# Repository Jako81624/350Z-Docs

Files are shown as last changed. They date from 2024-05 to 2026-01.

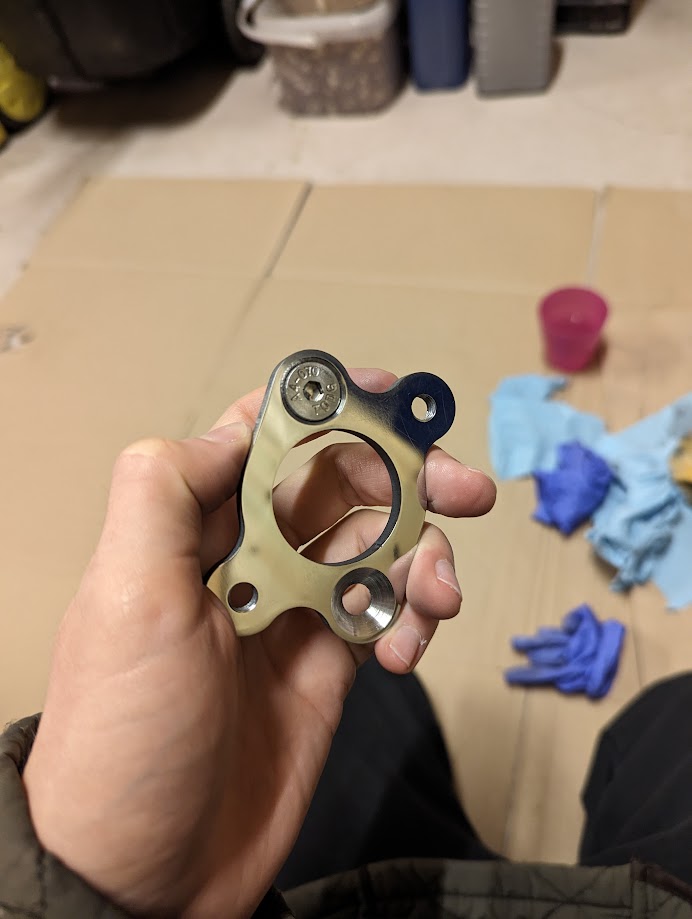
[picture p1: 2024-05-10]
Clutch-System/Master-Cylinder/Adapter-Plate-Front.jpg

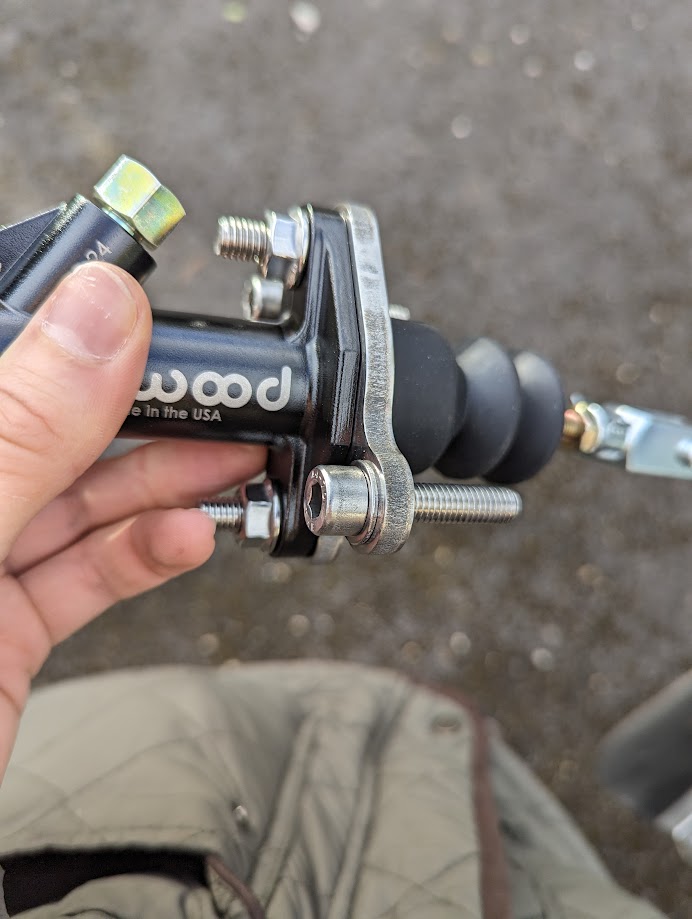
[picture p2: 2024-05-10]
Clutch-System/Master-Cylinder/Adapter-Plate-Rear.jpg

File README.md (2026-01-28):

# 350Z-Docs
Progressive documentation for undocumented areas of the 350Z - designed to increase longevity and democratize modification

When it comes to car modification, there is very little documentation for the little things.  A lot of crucial elements have been measured hundreds of times by many hundreds of people, but, for a variety of reasons, ranging from enclosure by private companies to sheer forgetfulness on the part of the individual, these crucial little tidbits are not public knowledge.

This repository was created purely with the intention of documenting all those useful bits and pieces.  If you have anything to add, please fork the repo and make a pull request.  Any additions are very much appreciated.

All files inside this repository are licensed under the Creative Commons CC-BY-SA 4.0 license (https://creativecommons.org/licenses/by-sa/4.0/) unless otherwise confirmed in direct correspondence with the repository creator.

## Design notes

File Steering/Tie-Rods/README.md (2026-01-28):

# HA (High-Adjust) Tie Rods
The files in this directory consist of all the components required to fabricate an outer tie rod (tie rod end) for the 350Z platform.

This is a somewhat novel design.  The shank component is inserted into the spindle and is secured by one flanged M12x1.25 nut (STEP file included under "Nuts", ISO standard).  This nut should be torqued to *at least* 34Nm in accordance to the FSM.  It is the opinion of some manufacturers that this is not enough torque, but without further testing I cannot take an educated stance.  One of the features of this design is a vertical, unthreaded section above the conical seat that extends to approximately one millimetre below the surface of the spindle.  This _should_ prevent catastrophic failure from over-torquing, but it is *NOT* a target, nor should it be relied on to prevent this.  There is a groove cut above the thread to house an 8mm E or C clip to prevent steering loss in the even that the retaining nut should back out.  It is *critical* that a thread locking compound is used with this retaining nut - "blue" strength compounds are recommended.  I recommend using the threaded misalignment spacers as jam nuts to torque down the retaining bolt.

**IMPORTANT NOTE** - The 350Z spindle is made from aluminium.  Over-torquing of the shank MAY result in the conical seat being dragged through the spindle receptacle, snapping it in half.  Older vehicles that have undergone many fatigue cycles (or have had replacement tie rod ends installed "enthusiastically" in the past) may have weakened receptacles.  Aluminium does not have a fatigue limit - any load applied will result in cumulative damage.  For all aluminium parts, failure is "when" and not "if".  For this reason, as of writing I recommend using the torque specification listed in the FSM (34Nm) and applying threadlocker.  Please check that this nut remains secure at several occasions less than 100 miles post-install, for the safety of yourself and others.

The turnbuckle is longer than most aftermarket offerings (as far as I am aware) at 95mm.  This is with the intention of ensuring maximum strength and thread engagement, but some edge cases may not be compatible.  If this is the case for you, the turnbuckle can be shortened by the requisite amount from the end housing the M14 thread in CAD.  One end is threaded for M14x1.5 - the thread diameter and pitch of the 350Z inner tie rods.  The other is threaded for M16x2.0.  Most 16mm-eye metric rod-end bearings on the market are built to this specification, as was the case for my chosen bearing; the SKF SAKAC 16M.  I encourage end users to use serviceable components - bearing coatings do not last forever and greasing them instead at your yearly inspection is easily done.  An M16x2.0 jam nut (ISO-4035 spec recommended) is required to "lock" the rod-end in to the turnbuckle.  A STEP file is provided under "Nuts".

The final components are the so-called "threaded misalignment spacers".  These are what make this kit "high-adjust".  There are two nuts - the top is thinner, the bottom thicker.  Both have an 18 degree chamfer on the flat face of one side.  The top nut is threaded on first with the chamfer on the underside.  This is followed by installing the rod-end bearing onto the 16mm shaft.  Finally, the bottom nut is installed with the chamfer on the topside (against the bearing).  These two nuts can then be adjusted to change the position of the rod-end bearing, which in turn will affect your steering geometry and "bump steer".  To eliminate bump steer to the best of your ability, ensure that your tie rods sit parallel with your lower control arms when the car is sat at ride height.  I do not yet know how far offset the bearing should be from the bottom of the spindle for a stock vehicle, but respected manufacturers (SPL) have it listed at half an inch, so I would start around there (18mm seems to be a close equivalent in comparison).  These documents will be updated when I have a more concrete measurement.

The TMS's do not have a torque spec other than *tight*.  Threadlocker is, once again, critical for safety.  Use it on the bottom TMS, even if you don't on the top.  In my case, SKF does not list a maximum compressive force for their bearings, and my material of choice was Grade 5 Titanium so I will be targeting 75Nm.  The only risk you face is deforming the bearing or shearing the shank in half.  Proceed with care!  Other fasteners under radial loads in the suspension area (brake caliper bolts, for example) are secured with bolts set to 88.3Nm, and the compression arms are secured at 84.5Nm.  Keep in mind that any inferences I make from that are purely "vibes-based", but that level of torque _feels_ suitable.

Addendum: The reason for the chamfer on the TMS's is to allow for maximum bearing misalignment.  The SAKAC 16M that I'm using has a rated misalignment of 15 degrees, so I made the chamfers at 18 degrees to allow the nuts to handily clear the bearing race.

## Material Choices
As previously mentioned, I used Grade 5 Titanium when making mine.  Other manufacturers have used 4000-grade alloy steels for theirs, and I can only assume that Nissan does something similar.  In the FEA that I carried out, I saw a single stress concentrator at or exceeding 950Mpa on the shank under the worst conditions imaginable (excessive pressure, unrealistic and enormous torque arm).  This is almost certainly an FEA artifact, but without further testing I can't confirm anything.  As such, I would err on the side of caution and use a material that exceeds 500Mpa.  I wouldn't expect loads to exceed even 200Mpa when used with under realistic installation conditions, but again, this is all theoretical.  Be safe and err on the side of caution.

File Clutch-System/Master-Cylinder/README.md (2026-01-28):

# Master Cylinder Adapter Plate
This adapter plate adapts the stock 350Z CMC mounting location (70mm PCD, 30deg off-centre) to the vertically aligned Wilwood/Tilton type mounts.

If all you want is the adapter, send the DXF file to your laser cutting service of choice (6mm thick steel or metal of your choice).  You will need to tap the off-centre holes (firewall holes) for an M8 thread and countersink the vertically aligned holes (on the side against the firewall) as to both mount the aftermarket cylinder to the adapter using countersunk M8 head-socket bolts and to install two 30 or 35mm fully-threaded M8 socket head bolts into your freshly tapped threads (I recommend some blue threadlock to stop them backing out) and install the assembled unit in the stock location.  Pictures are in the repo for guidance.

It is likely that the fit in the bolt holes will be tight.  Persevere, it will install snug.

You will almost certainly need to replace the stock clutch line to accomodate an aftermarket CMC.  Measurements and fittings for those lines are in Hydraulic-Lines folder one directory up from here.  If in doubt, use a banjo bolt.

CC-BY-SA 4.0

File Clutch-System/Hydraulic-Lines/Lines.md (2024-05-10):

## Clutch Hydraulic Lines
When upgrading the clutch, it is quite common that supplemental modification to the hydraulic components will be required too.  In regards to the HR-generation, the CSC (Concentric Slave Cylinder) is known to have a limited lifespan - though replacing it with an aftermarket unit tends to rememdy this issue, and some aftermarket clutch manufacturers create kits that are designed for use with OEM/OEM-Style CSCs (OS Giken, for example).

TODO: Add dimensions and sketch of slave cylinder

At the other end of the system is the master cylinder.  Details below:

    DE+:
        Bore: 
        - 5/8"in

    HR:
        Bore: 
        - 11/16"in

    All:
        Thread Size and Pitch:
        - M10x1.0
        Clutch Feed Hose Size:
        - 8AN

TODO: Move these to their own dedicated section

The clutch lines in the 350Z are notorious for being difficult to bleed.  This will lead a lot of people to replacing them.  In stock form, both the pre-HR and HR generation use four clutch lines.  The first leads to the clutch damper located in the front-left wheel-well behind the rearwards plastic shroud.  The second leads from the aformentioned damper, to a bracket underneath the car.  This bracket is what starts the third section - this time using flexible hose.  The final section is a short and arguably redunant hardline run that exits the flexible hose and performs a u-turn to go back into the CSC termination block.  As of writing, my experience is with the HR generation, and in this case the flexible hose is secured at both ends with horseshoe clips to a bracket on the chassis and the gearbox respectively.

The clutch lines are all threaded in M10x1.0.  When replacing the clutch lines, some will opt to replace only the soft line and leave the hardline in place.  There are many kits out there that achieve this, and, in the case of the HR, the length of the flexible section will be no longer than approximately 30cm (data sourced from UKDM RHD vehicle).

Hose Details:

    DE+:
        - Unknown, please fork and submit a pull req if known
    HR:
        Lengths:
            Short (Flexi):
            - Approx. 30cm
            Combined run (CMC to CSC termination block)
            - Approx. 228cm

        Fittings:
            Short (Flexi):
            - 2x Female M10x1.0 Circlip Fittings
            Short (Flexi to CSC termination block):
            - M10x.10 Male (Convex lip, flexi end) to M10x1.0 Male (Concave lip, termination block end)
            Hard Line (CMC to Damper)
            - M10x1.0 Male to M10x1.0 Male
            Hard Line (Damper to Flexi)
            - M10x1.0 Male to M10x1.0 Male

Many people will replace the master cylinder with an aftermarket unit when using heavier aftermarket clutches.  There is no adjustment to be made in hydraulic system.  Clutch "bite" and modulation is a function of the throw distance between the face of the CSC and your pressure plate and the bore/displacement of your master cylinder.  Clutch "weight" is a function of pressure plate strength and CSC/CMC bore.  This being said, it is *possible* to make some minor adjustments to the height of your clutch pedal by winding in the clevis on your master cylinder, and winding out either your upper clutch stopper on cars unequipped with cruise control or your clutch ASCD on cruise-equipped vehicles.  Both are located in the same place.  This will **NOT** change the characteristics of your clutch - just the height of your pedal.

There are a couple of methods by which you can adjust the modulation of your clutch. One is by changing the bore ratio between the CSC and CMC i.e. a smaller bore CMC will require less foot pressure and will displace less clutch fluid per unit distance.  The obvious warning here is that you will have to ensure that your CMC can displace _enough_ fluid to fully disengage your clutch, or you risk damaging your clutch and/or being unable to disengage the transmission from the engine entirely.  Displacement of the stock CMC is currently not documented, but based on aftermarket units I perform my calculations with 1.25" of travel.  The other option is to design a mechanism by which you can adjust the ratio of pedal to CMC plunger movement.  For example, attaching the CMC plunger closer to the point of pedal rotation would result in less lateral movement - however, this would have the unintended side-effect of actuating the plunger at an extreme angle and potentially accelerating wear significantly.  If a design comes to fruition, it will be documented here.

Common replacements for CMCs include both Tilton and Wilwood.  Dimensions are available from the manufacturer for fabricators.  Dimensions of the stock CMC will be included here when they have been obtained.  The PCD is larger than the Wilwood GS Remote as of the time of writing, and the firewall bolts appear to approximately be rotated at a 20 degree angle from the horizontal plane.  CAD drawings and adapter plates will be open sourced and included here when completed.

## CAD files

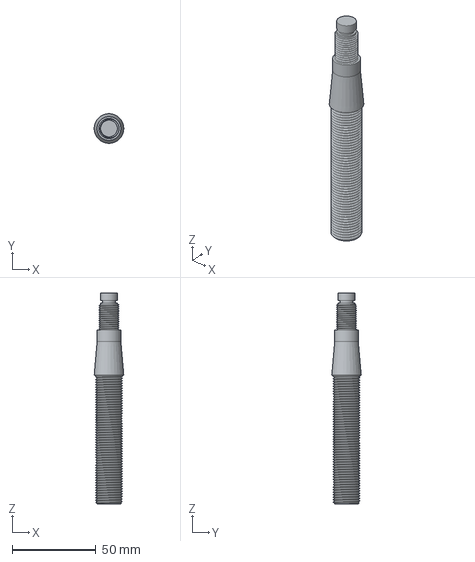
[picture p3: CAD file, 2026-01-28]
Steering/Tie-Rods/Shank/Shank-SingleCurve-FullThread.step
17.7 x 17.7 x 125.9 mm

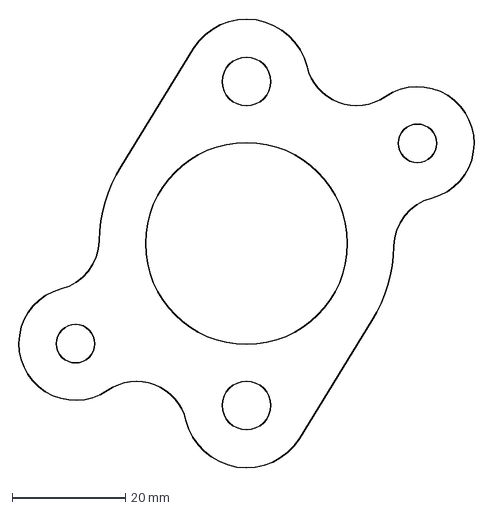
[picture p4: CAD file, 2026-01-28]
Clutch-System/Master-Cylinder/350ZMasterCylinderWilwoodAdapterV2-Sketch.dxf
81.4 x 80.3 mm

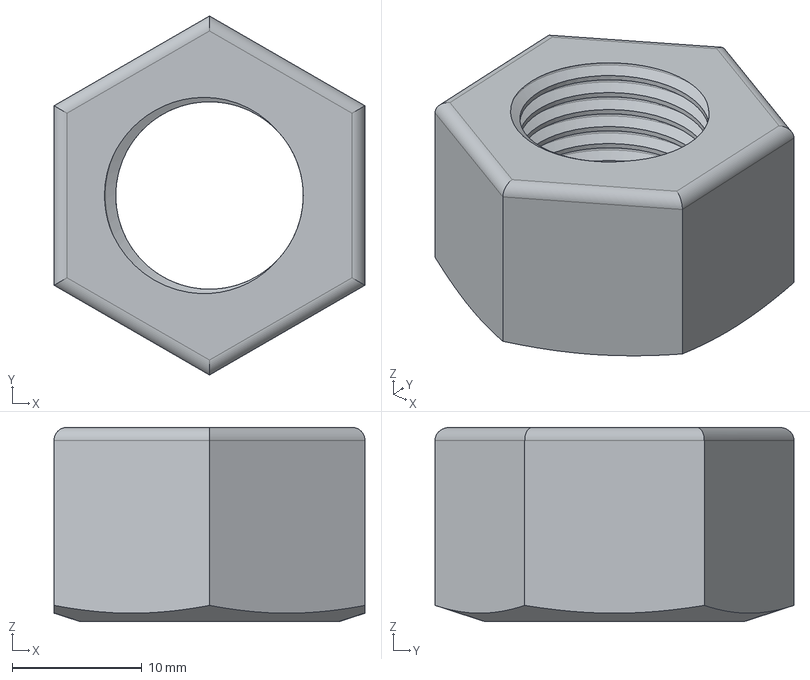
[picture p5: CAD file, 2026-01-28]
Steering/Tie-Rods/Misalignment Spacer/Bottom/CNC/Threaded Misalignment Spacer Bottom - CNC.step
24.0 x 27.7 x 15.0 mm

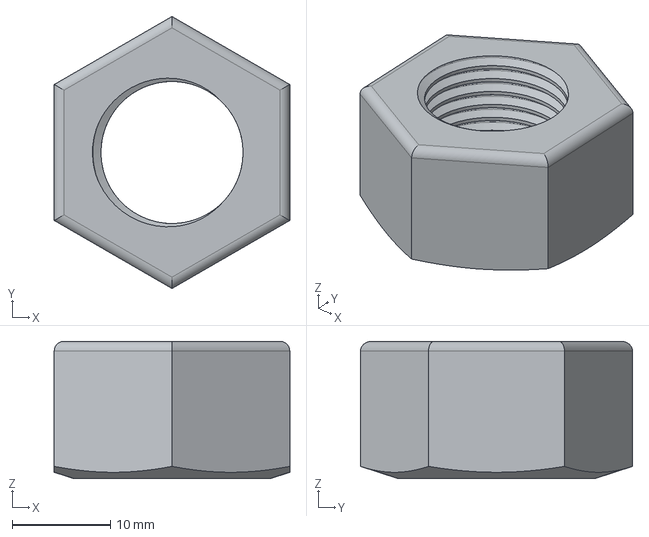
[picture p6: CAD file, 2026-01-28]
Steering/Tie-Rods/Misalignment Spacer/Bottom/Threaded Misalignment Spacer Bottom.step
24.0 x 27.7 x 14.0 mm

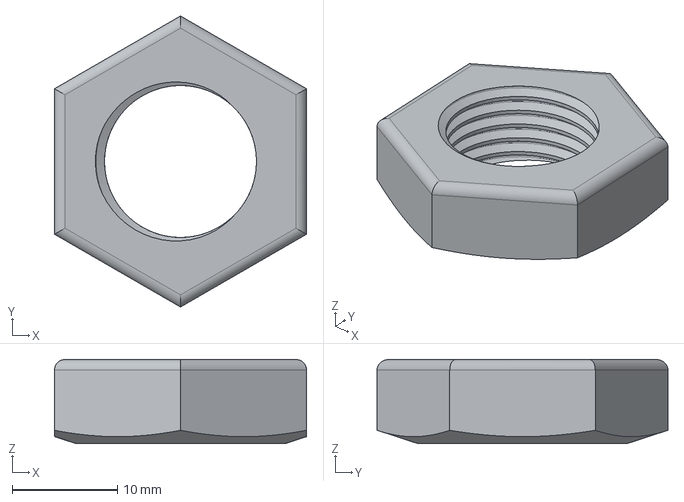
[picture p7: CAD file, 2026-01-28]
Steering/Tie-Rods/Misalignment Spacer/Top/CNC/Threaded Misalignment Spacer Top - CNC.step
24.0 x 27.7 x 8.00 mm

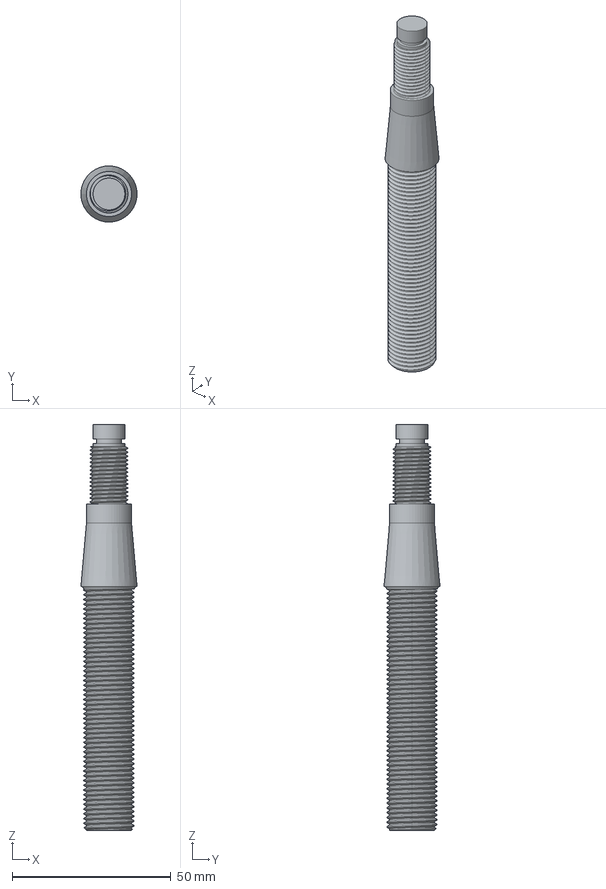
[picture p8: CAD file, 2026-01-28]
Steering/Tie-Rods/Shank/CNC/Shank-CNC.step
17.7 x 17.7 x 127.9 mm

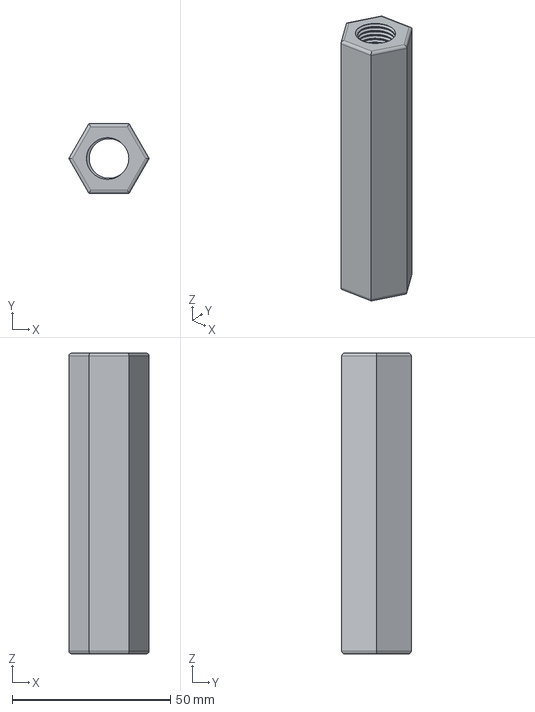
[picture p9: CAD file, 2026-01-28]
Steering/Tie-Rods/Turnbuckle/CNC/Turnbuckle-CNC.step
25.4 x 22.0 x 95.0 mm

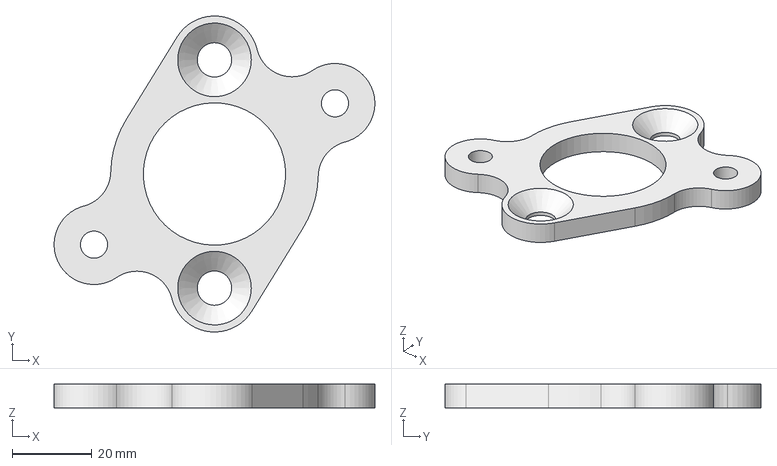
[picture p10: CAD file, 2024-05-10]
Clutch-System/Master-Cylinder/350ZMasterCylinderWilwoodAdapterV2.FCStd
80.4 x 79.2 x 6.00 mm

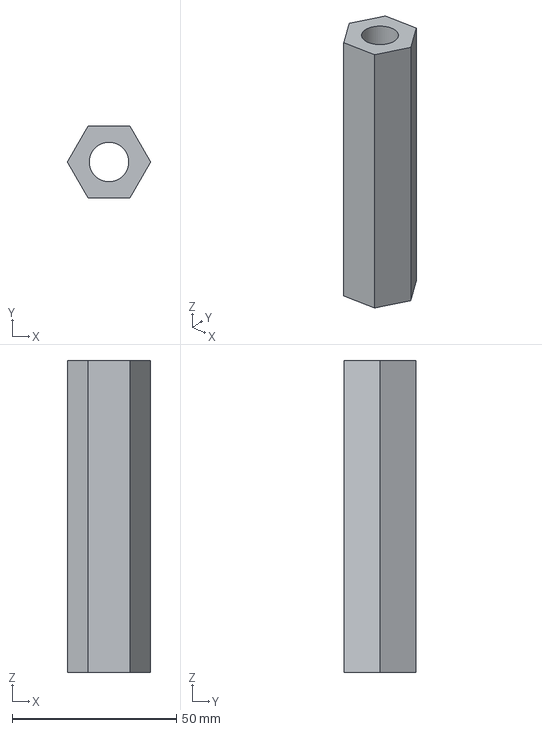
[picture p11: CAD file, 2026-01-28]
Steering/Tie-Rods/Turnbuckle/Turnbuckle-Unthreaded.step
25.4 x 22.0 x 95.0 mm

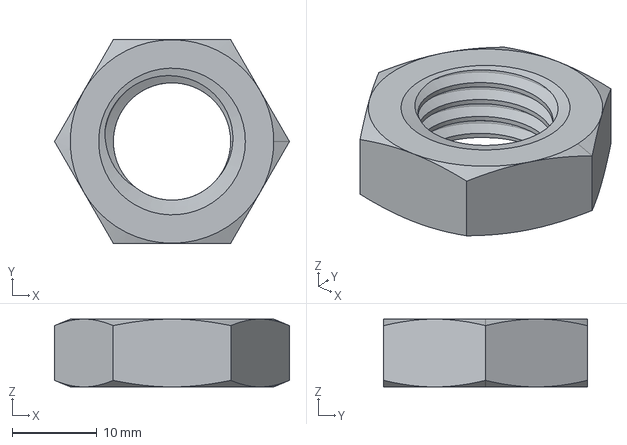
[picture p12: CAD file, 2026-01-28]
Steering/Tie-Rods/Nuts/M16x2.0-Nut-ISO4035.step
27.7 x 24.0 x 8.00 mm

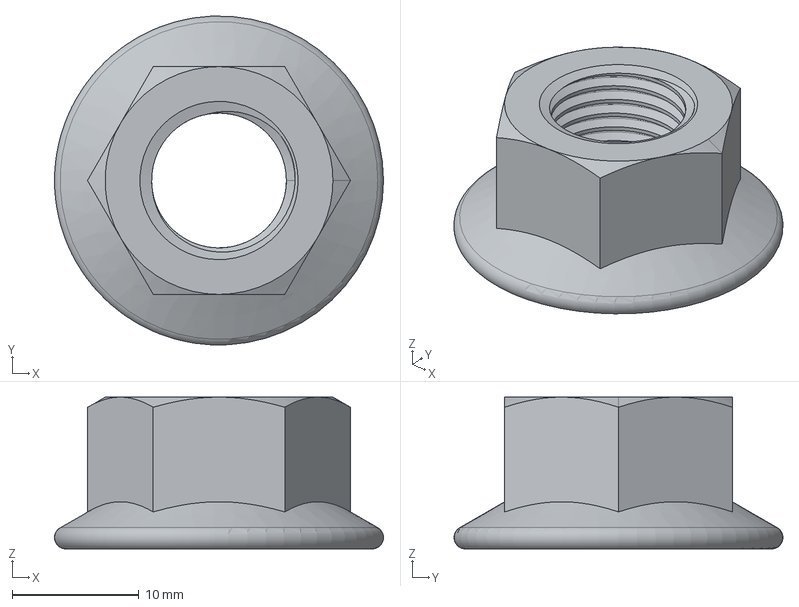
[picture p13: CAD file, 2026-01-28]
Steering/Tie-Rods/Nuts/M12x1.25-Nut-Flanged.step
26.0 x 26.0 x 12.0 mm

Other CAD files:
Steering/Tie-Rods/Misalignment Spacer/Top/Threaded Misalignment Spacer.FCStd
Steering/Tie-Rods/Shank/Shank.FCStd
Steering/Tie-Rods/Turnbuckle/Turnbuckle.FCStd
Steering/Tie-Rods/Misalignment Spacer/Top/Threaded Misalignment Spacer-Threaded.step
Clutch-System/Master-Cylinder/350ZMasterCylinderWilwoodAdapterV2-Chamfer.obj
Steering/Tie-Rods/Turnbuckle/Turnbuckle-Threaded.step
Steering/Tie-Rods/Misalignment Spacer/Bottom/CNC/Threaded Misalignment Spacer Bottom - CNC.FCStd
Steering/Tie-Rods/Misalignment Spacer/Bottom/Threaded Misalignment Spacer Bottom.FCStd
Steering/Tie-Rods/Misalignment Spacer/Top/CNC/Threaded Misalignment Spacer Top - CNC.FCStd
Steering/Tie-Rods/Shank/CNC/Shank-CNC.FCStd

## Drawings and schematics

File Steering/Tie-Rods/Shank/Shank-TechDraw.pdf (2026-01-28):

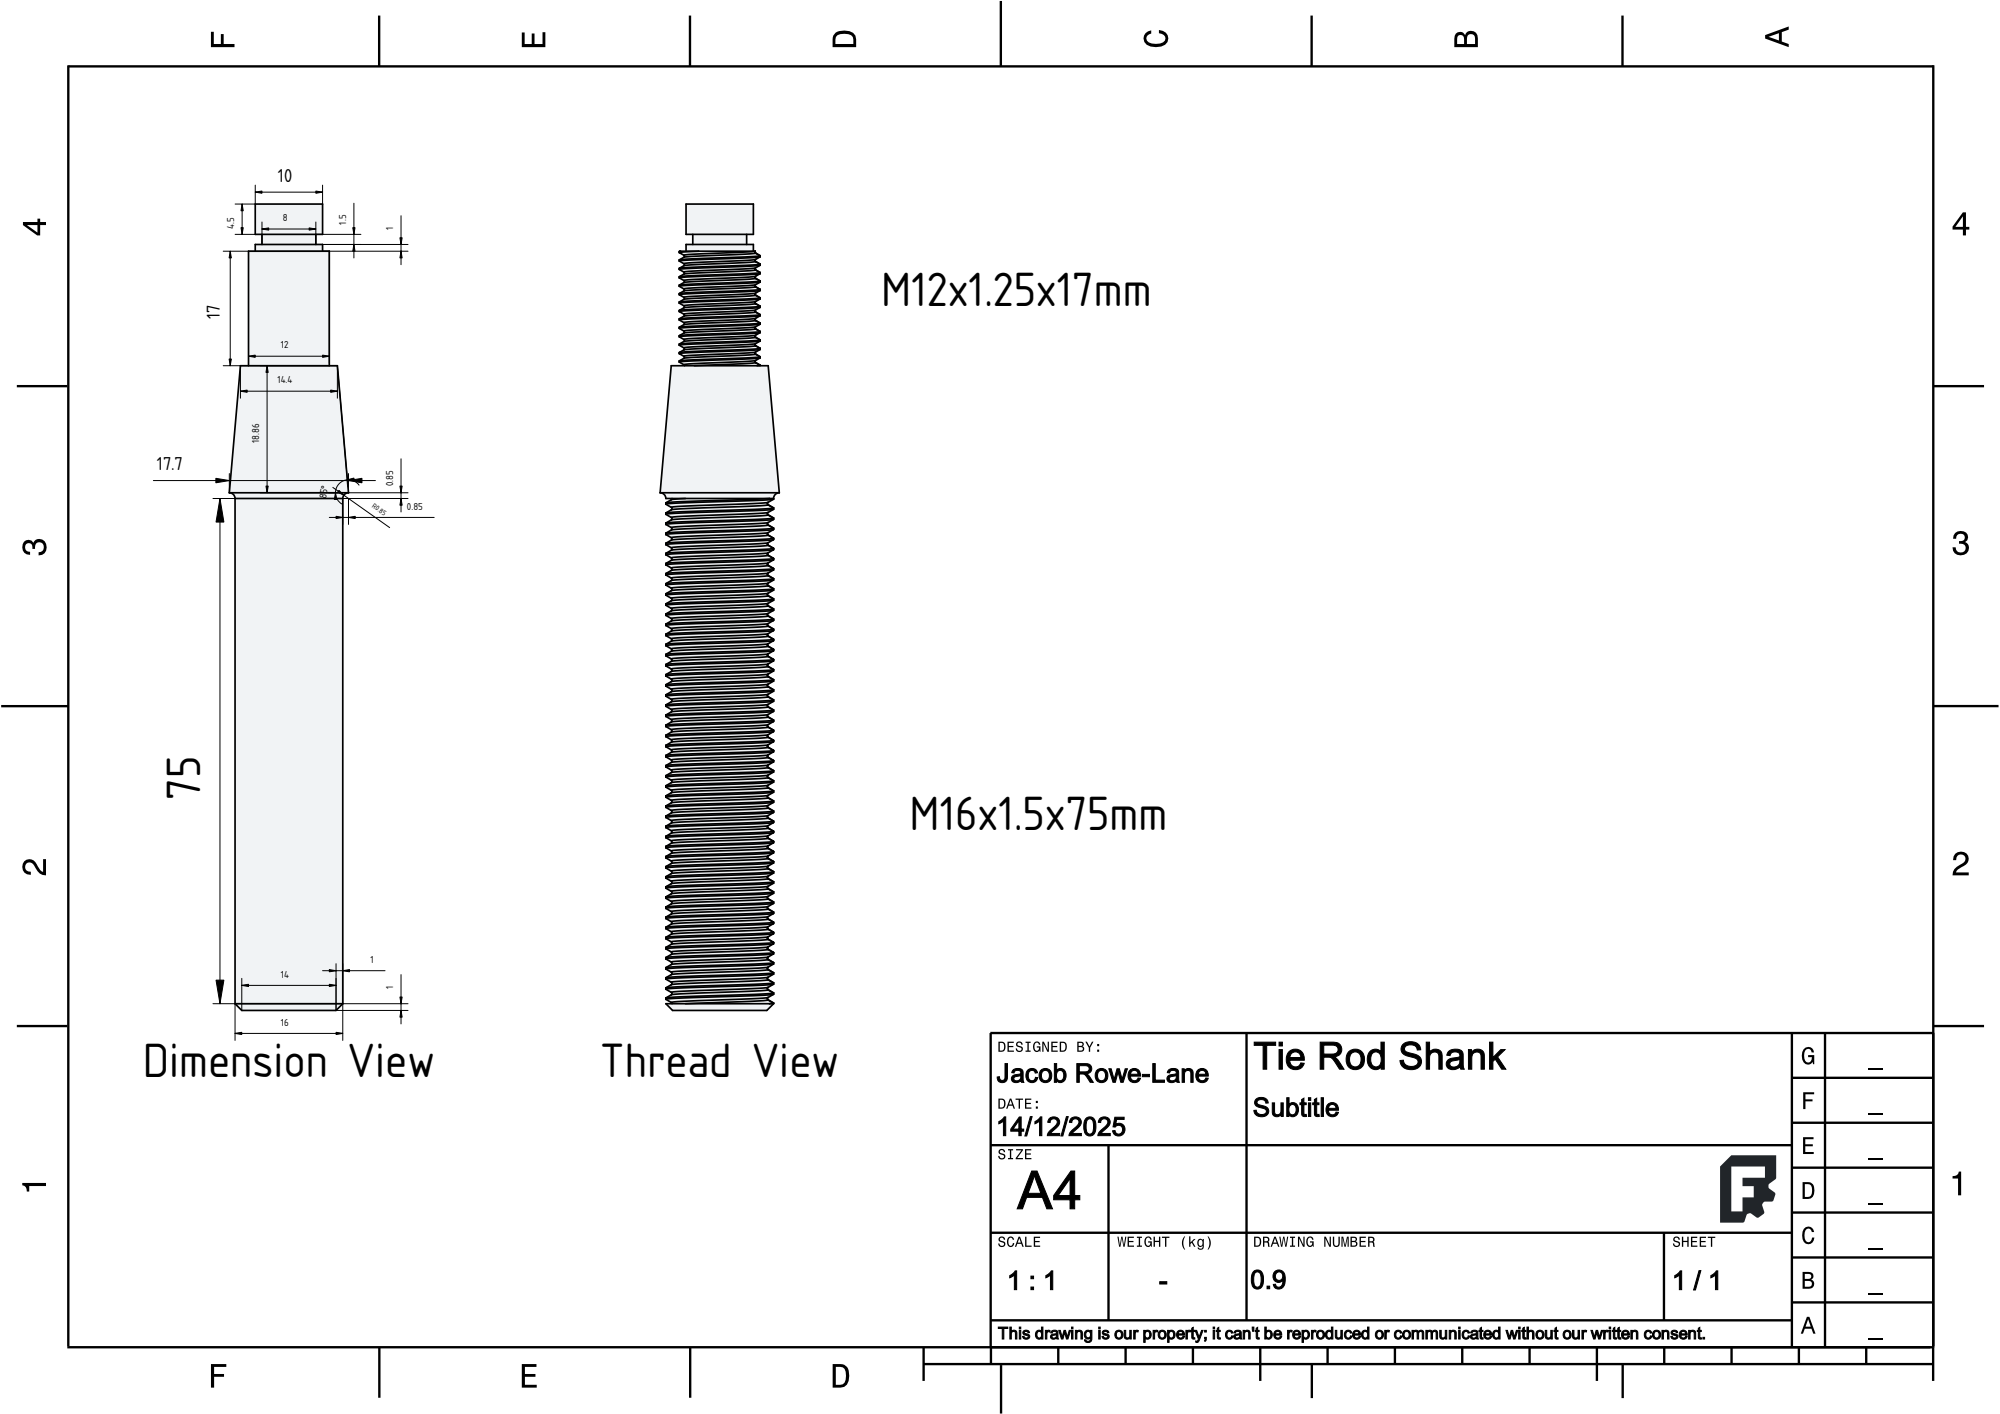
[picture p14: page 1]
Dimension View; Thread View

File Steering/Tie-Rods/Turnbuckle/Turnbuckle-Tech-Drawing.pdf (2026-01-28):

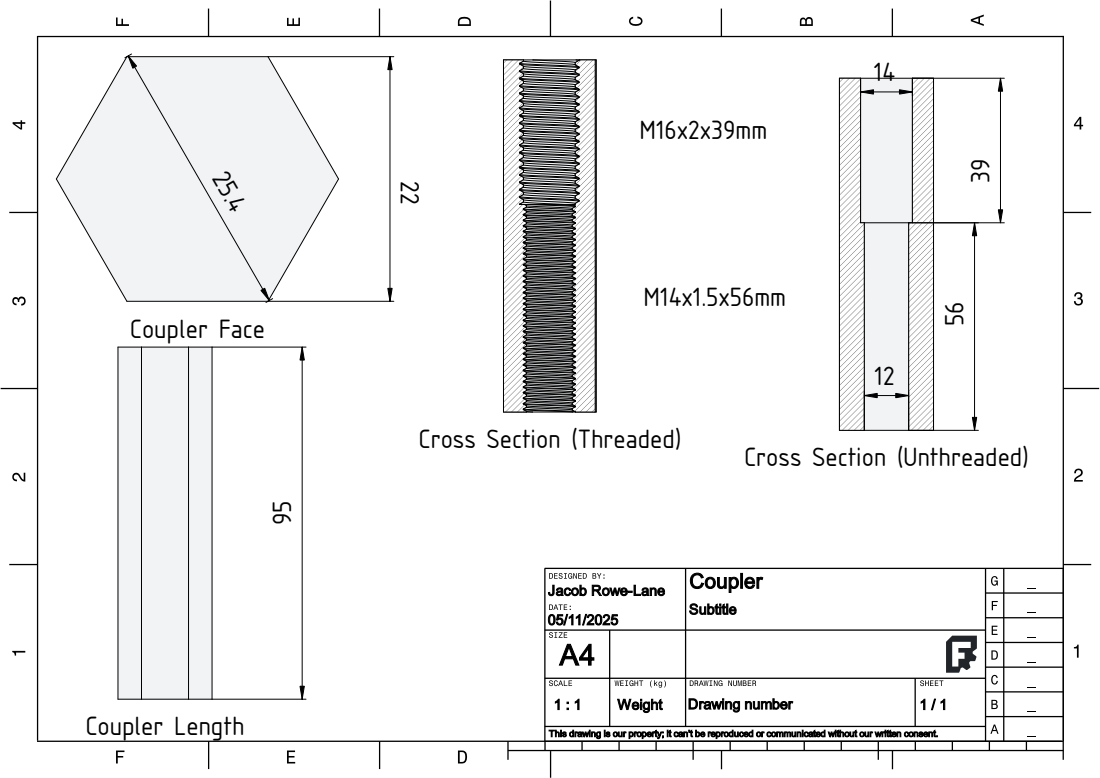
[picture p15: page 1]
Coupler Face; Coupler Length

Cross Section (Threaded)

Cross Section (Unthreaded)

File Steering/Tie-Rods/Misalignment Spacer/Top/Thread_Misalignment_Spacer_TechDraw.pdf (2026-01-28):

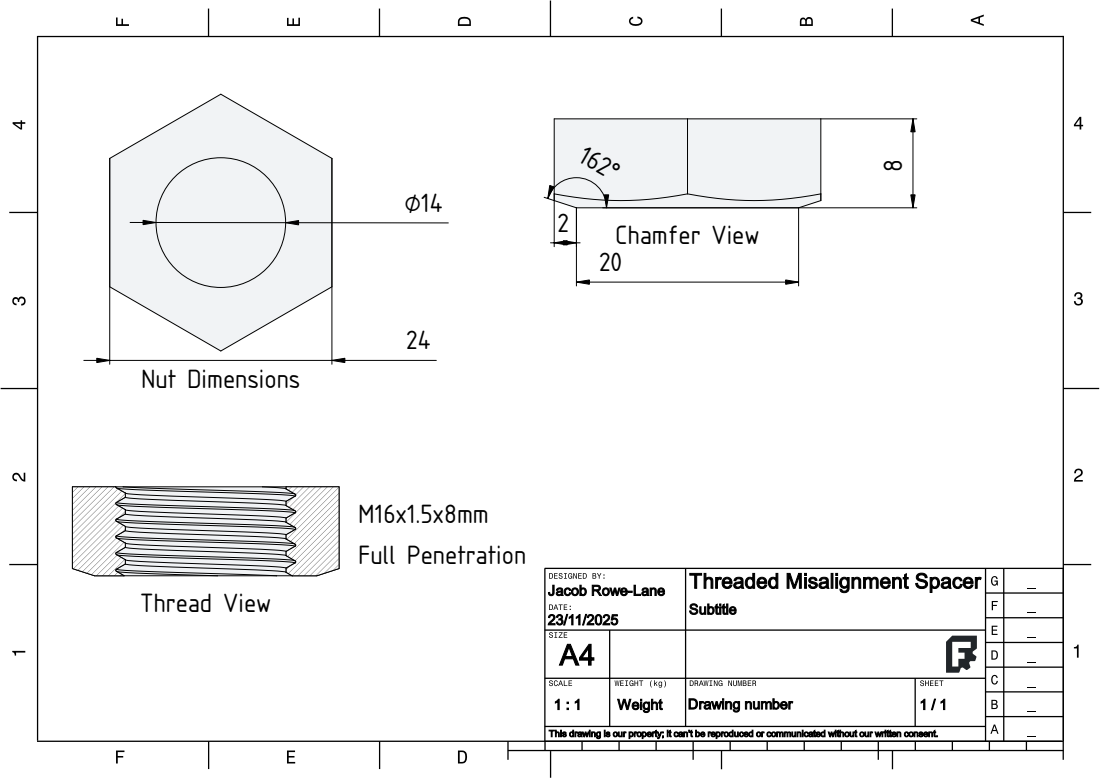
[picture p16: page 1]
Nut Dimensions; Chamfer View; Thread View; Full Penetration

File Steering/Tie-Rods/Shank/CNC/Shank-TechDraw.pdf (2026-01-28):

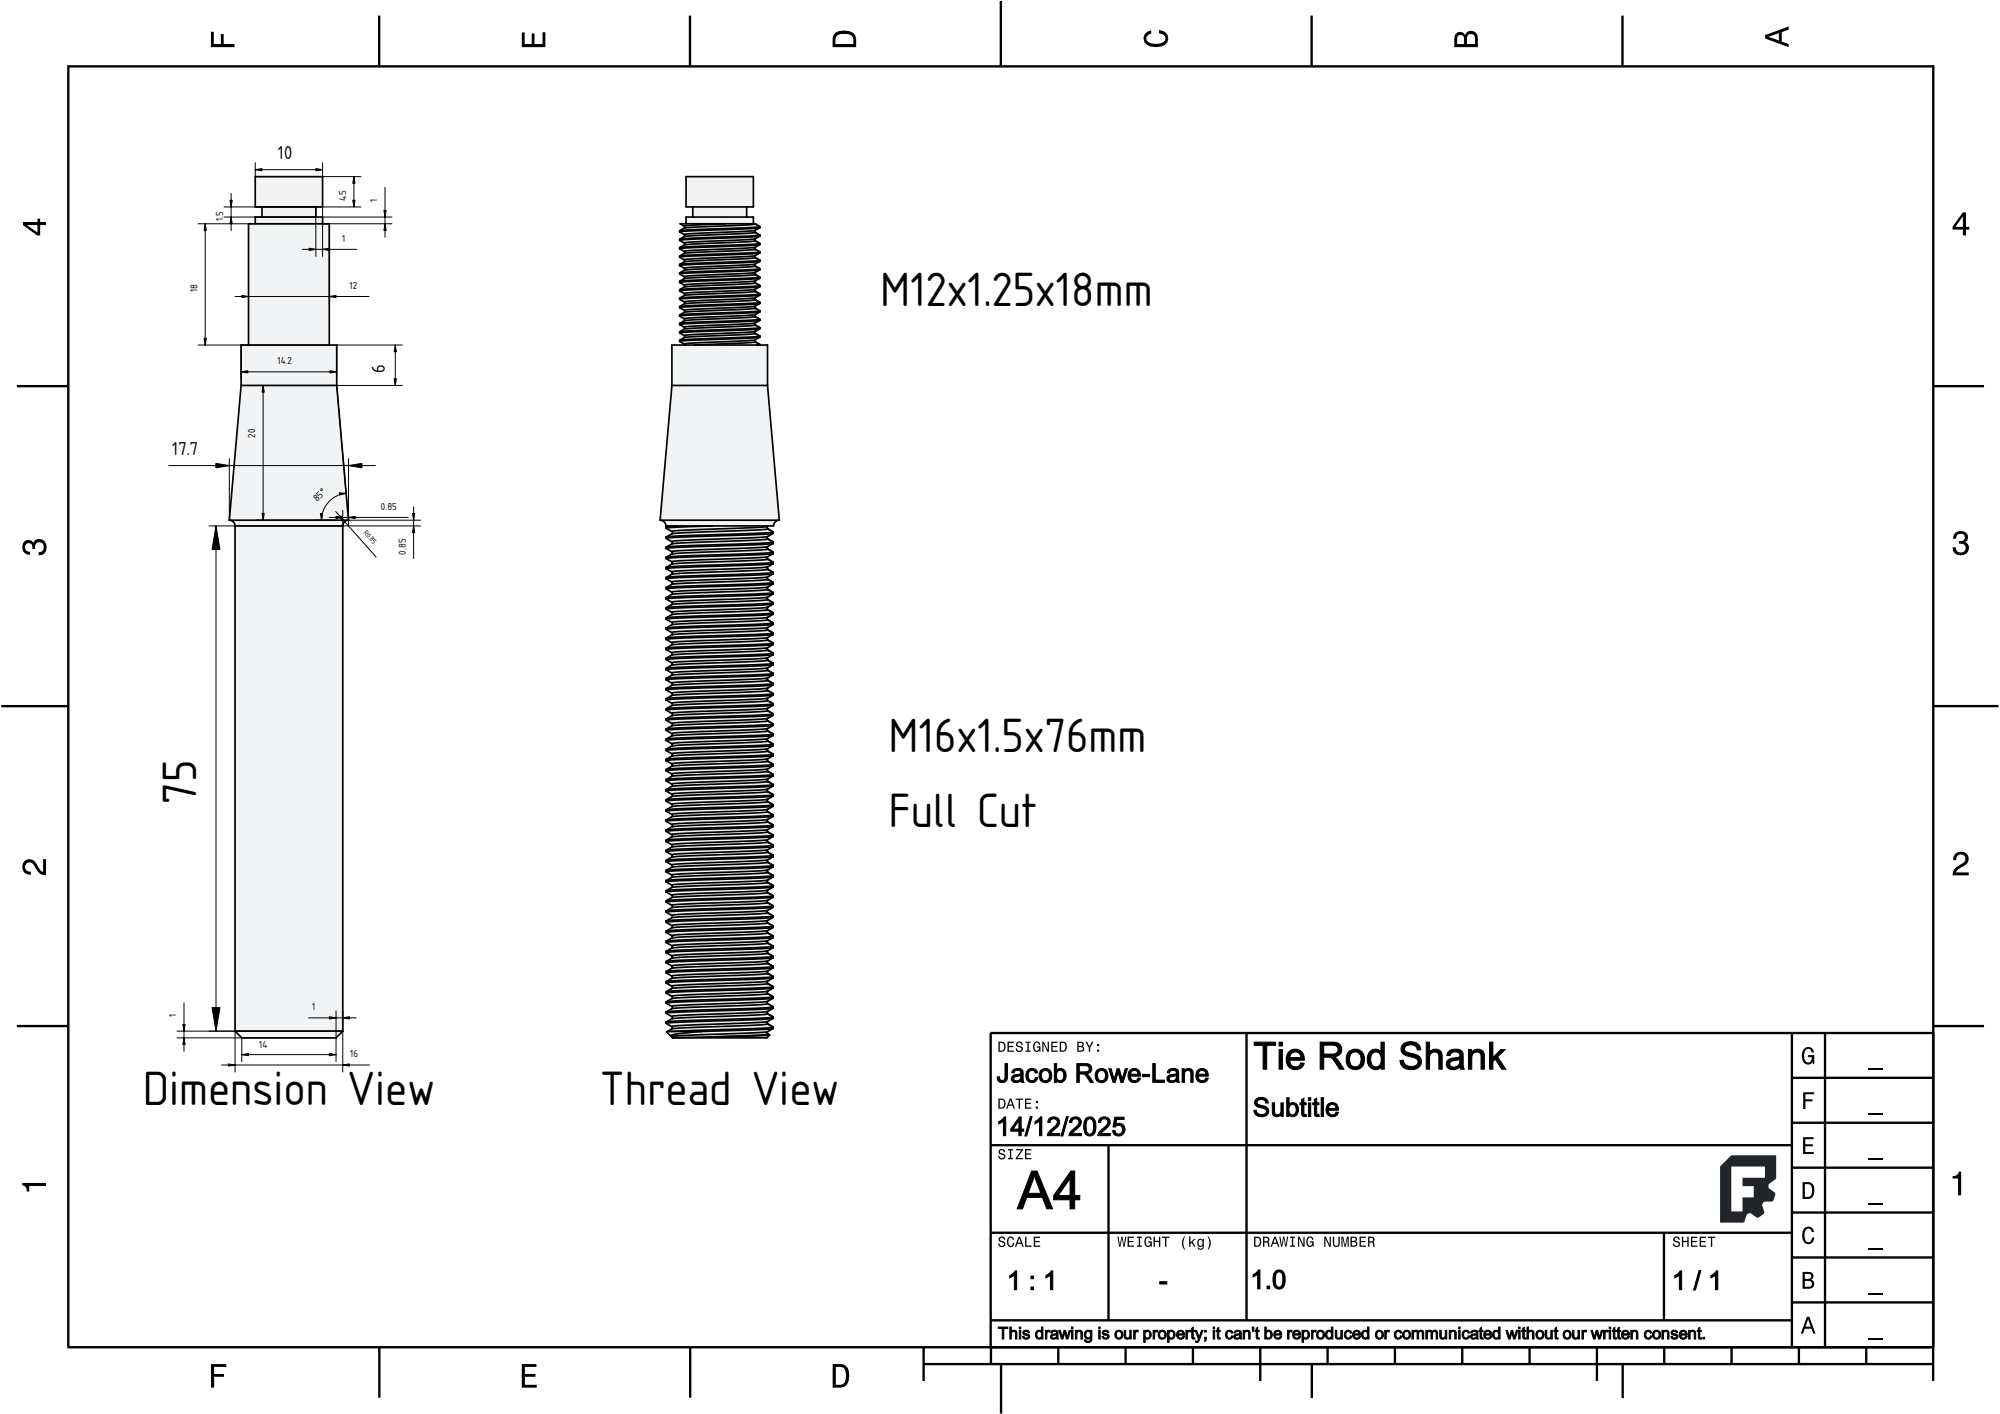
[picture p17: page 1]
Dimension View; Thread View; Full Cut

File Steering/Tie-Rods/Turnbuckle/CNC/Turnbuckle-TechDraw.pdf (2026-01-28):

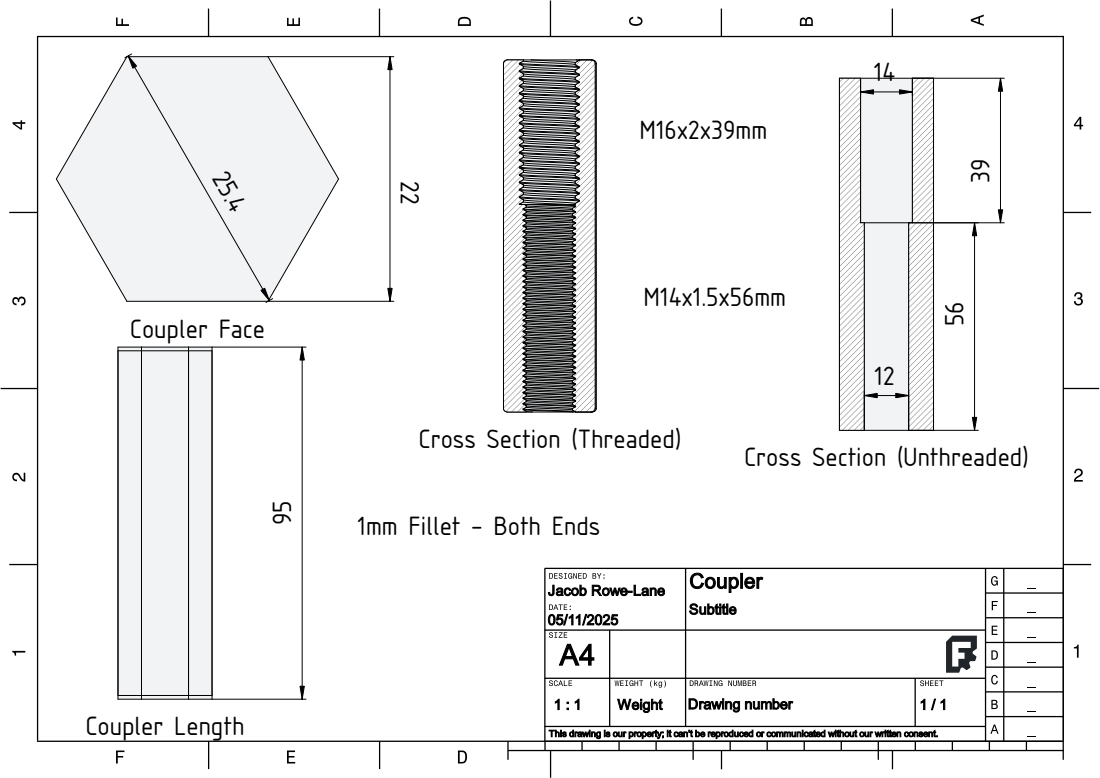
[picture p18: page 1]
Coupler Face; Coupler Length

Cross Section (Threaded)

Cross Section (Unthreaded)

1mm Fillet - Both Ends

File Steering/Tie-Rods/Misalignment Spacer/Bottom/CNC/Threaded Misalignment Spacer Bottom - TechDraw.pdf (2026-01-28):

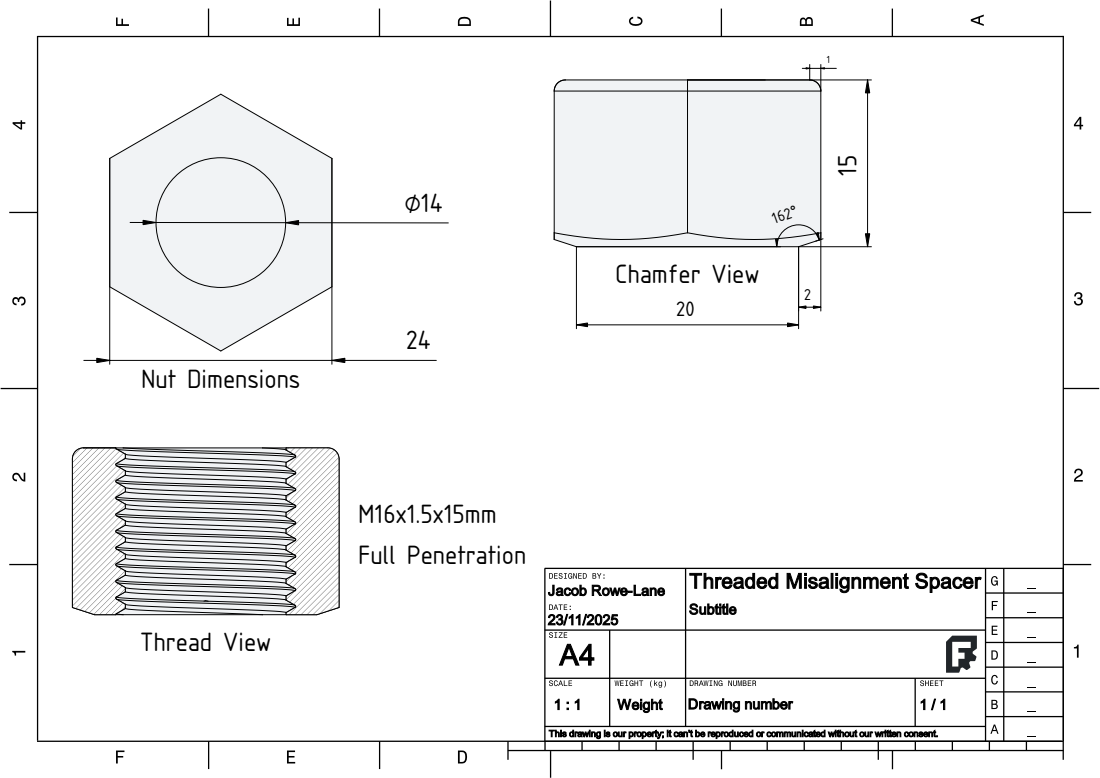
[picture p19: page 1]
Nut Dimensions; Chamfer View; Thread View; Full Penetration

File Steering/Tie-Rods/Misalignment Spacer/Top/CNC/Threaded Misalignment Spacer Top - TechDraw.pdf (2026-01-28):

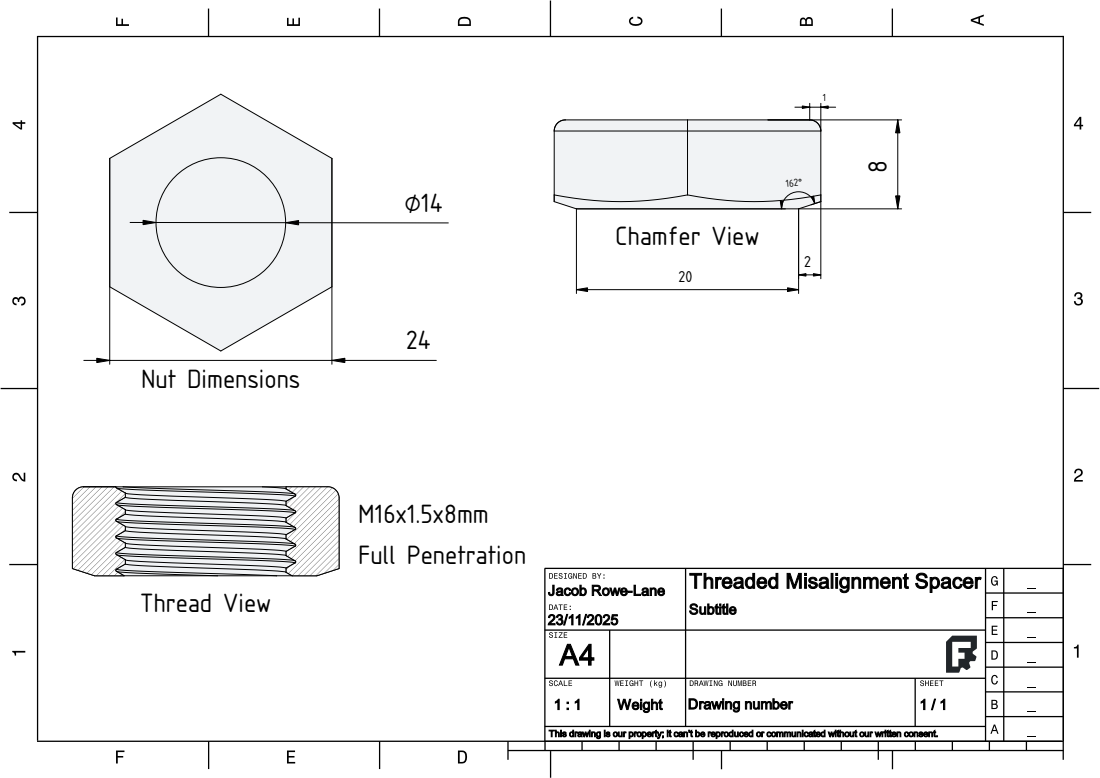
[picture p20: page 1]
Nut Dimensions; Chamfer View; Thread View; Full Penetration

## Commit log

2024-03-01 Formatting issue in hydraulics section r.e. bolt thread/pitch
2024-05-10 Upload Wilwood/Tilton Style Adapter Plate CAD
    [350ZMasterCylinderWilwoodAdapterV2-Chamfer.obj, 350ZMasterCylinderWilwoodAdapterV2-Sketch.dxf, 350ZMasterCylinderWilwoodAdapterV2.FCStd]
2024-05-10 Add directions regarding replacing stock clutch lines r.e. Master Cylinder
2026-01-28 Added High-Adjust Tie Rod End design files and README
    [350ZMasterCylinderWilwoodAdapterV2-Sketch.dxf, M12x1.25-Nut-Flanged.step, M16x2.0-Nut-ISO4035.step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]
2026-01-28 Added material recommendations to HA-TRE
